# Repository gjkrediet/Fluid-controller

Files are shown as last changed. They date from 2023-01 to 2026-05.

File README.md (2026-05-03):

# Fluid-controller
A wireless battery powered pendant for FluidNC based on esp32



This controller uses bluetooth for communication. Be aware that bluetooth and wifi can not be used at the same time and, in fact, need different fluid-nc firmwares.  Sardar Azari seems to have adapted the controller to communicate via tcp. Take a look at https://github.com/AC8L/FluidNC-Pendant

# Main functions
Display shows: 
Machine coördinates, Work coördinates, Spindle speed and state, Set speed and step size when using joystick and rotation encoder, Overrides (Speed, Feed, Rapid),	Machine state, Battery state, Current buttons functions

Main functions buttons, joystick and dial: 
Wake up, Jog gantry and spindle via joystick and/or dial, Set Jog step size and speed via dial, Set spindle speed and switch on/off,	Set overrides (Speed, Feed, Rapid),	Cancel/abort job.

Main functions menu: 
Home machine, Zero workcoördinates, Go to zero, Probe.

# Hardware
1. LilyGO TTGO T-Display V1.1 which is a developmentboard with an ESP32, with a built-in tft (IPS) display and battery-charger. I purchased it for about €13 from internet.
2. Rotary encoder / dial (about €1)
3. Three colored buttons NO (total of €2)
4. PSP joystick (about €3)
5. Lion 18650 battery (€7)
6. Single-sided pcb
7. some pieces of wire (preferably different colors) of which five have female dupont-connectors
8. PLA (25 meter)
9. 8 screws M3 x 8

# Schematic and PCB

The pcb only holds the TTGO developmentboard and the rotary-encoder. The other components are mounted on the lid and wired to the pcb. The schematic of the pcb (in Kicad) is therefore very simple. The isolation-routing of the PCB was done with the very same CNC-router I made this controller for. To fit in the joystick, a corner of the PCB had to be sawed of (Later I updated the edge-cuts in Kicad so now the design should be OK).

The three buttons are at one side connected to the ground (all to J1.1) and are connected tot J1.2, J1.3 and J1.4 respectively.
The joystick is connected tot J2 with J2.2 unconnected (Because I later decided to wire the VCC of the joystick to an output-pin).

# Programming

Programming is done in Arduino IDE. All code exists in one single file. Most constants are enumerated or set with defines at the beginning. I hope it will explain itself to some extent.

Compile with partition scheme minimal SPIFFS or it will not fit.

# Case

pendantV2case_lid2
pendantV2lid_case

# Assembly

Schematic drawing of the lid with positioning of the components (excl. battery).

afbeelding

Female headers and the rotary encoder are soldered on the pcb. The other components are connected to the PCB with wires. Plus and minus wires are directly soldered to the battery and connected to the TTGO with a JST-connector.

inside1

To further reduce the powerconsumption I decided to feed the joystick via an outputpin of the esp32, which is why you see the red wire soldered on later.

inside2

The battery is wired to the JST-connector on the TTGO

# How to operate

The functions of the pendant were tailored to my needs. Below an oversight of the functions of the various buttons and button-combinations and the menu-options. It might be somewhat cryptic but I hope it may help.

JS=Joystick, BD=dial, BR=red button, BG=green button, BY=yellow button

Switch the pendant on: press JS

Reset the pendant: press JS

The pendant powers off after some time when idle or via the appropriate menu-option.

The pendant can either be in home-state (PH) or menu-state (PM).

Function of the dial-knob can be changed by rotating the dial while pressing BG.

Functions can be (default is DJ; function is indicated on the display with a blue circle):
- DX: Jog 1 step X-axis
- DY: Jog 1 step Y-axis
-	DZ: Jog 1 step Z-axis
-	DS: Set spindle-speed
-	DJ: set jogspeed and step-size
-	DOF: set override Feed
-	DOS: set override Speed
-	DOR: set override Rapid

The function of the buttons depend on the machine-state (MS, shown in the middle of the display of the pendant; function of BR, BG, BY shown on the bottom line of the display). They are as follows.

PH:
  -	JS + MS=Idle or MS=Jog:
    -	Up/down: jog Y-axis
    -	Left/Right: jog X-axis
  -	JS + MS=Idle or MS=Jog + BR (keep pressed)
    -	Up/down: jog Z-axis
    -	Left/Right: no function
  -	BG: enter PM
  -	BY: abort machine-operation
  -	BG (keep pressed) + BD: Change function dial-knob
  -	BR + MS=Alarm: Unlock Machine
  -	BR + DS: Spindle on/off

PM:
  -	BD: navigate menu (poweroff, spindlespeed, spindle on/off, small/large steps for changing jogspeed/stepsize, exit menu, home the machine, Set current Work XY-position to zero, Set current Work Z-position to zero, Probe Z-axis, Jog machine to XY-position zero, unlock Machine (grbl), reset Machine (grbl), Set and save brightness).
  -	BG: confirm menu-choice
  -	BR: Cancel
  -	BR (long press): poweroff

## OTA
Powering on the pendant while keeping the the red button pressed will start Wifi and activate OTA (Over The Air programming from within the Arduino IDE).

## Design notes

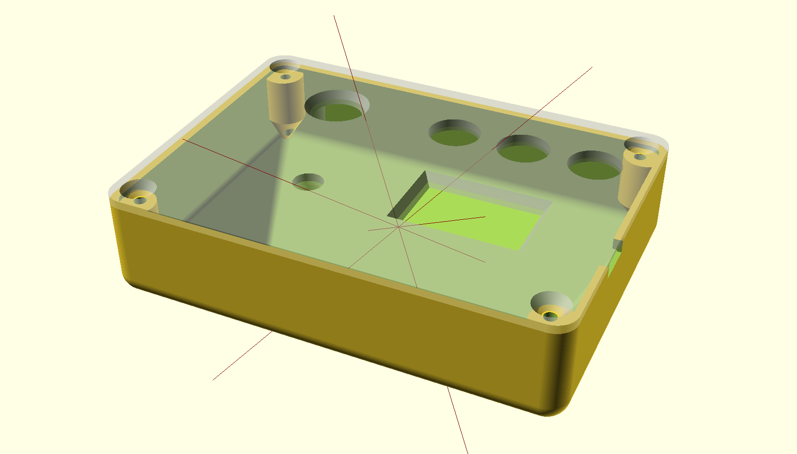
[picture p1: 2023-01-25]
case/pendantV2case_lid.png

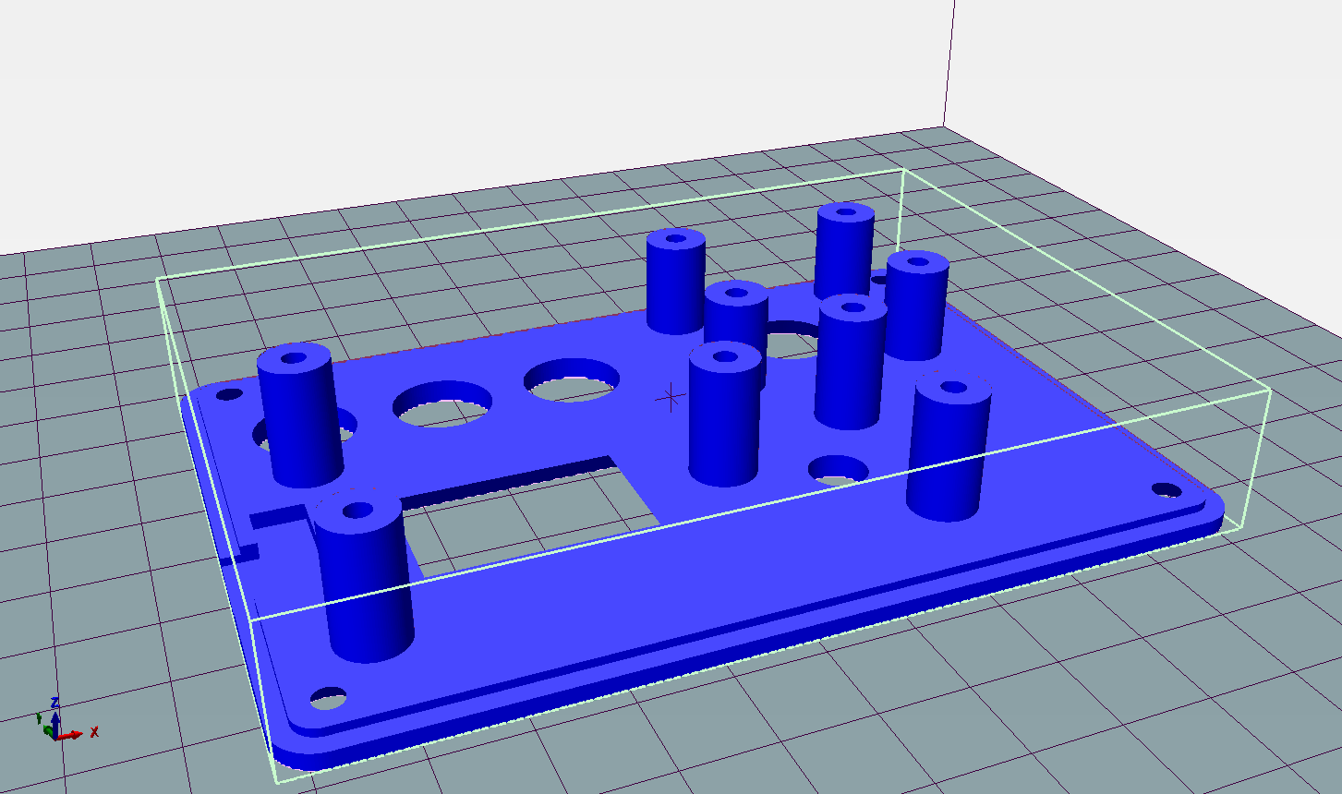
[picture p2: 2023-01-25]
case/pendantV2lid_stl.png

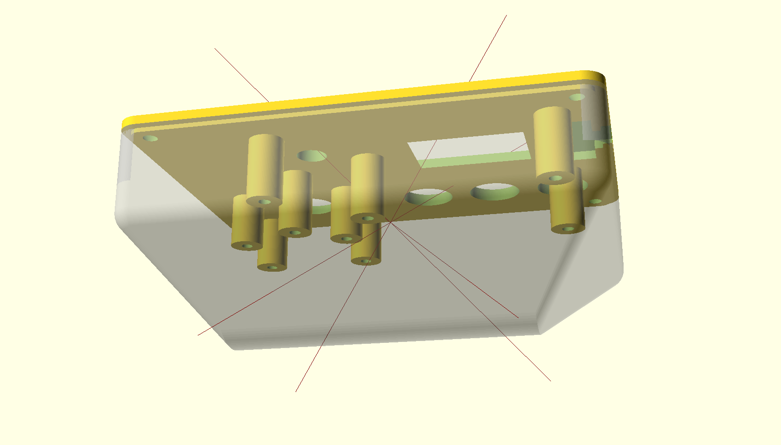
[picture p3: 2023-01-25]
case/pendantV2lid_case2.png

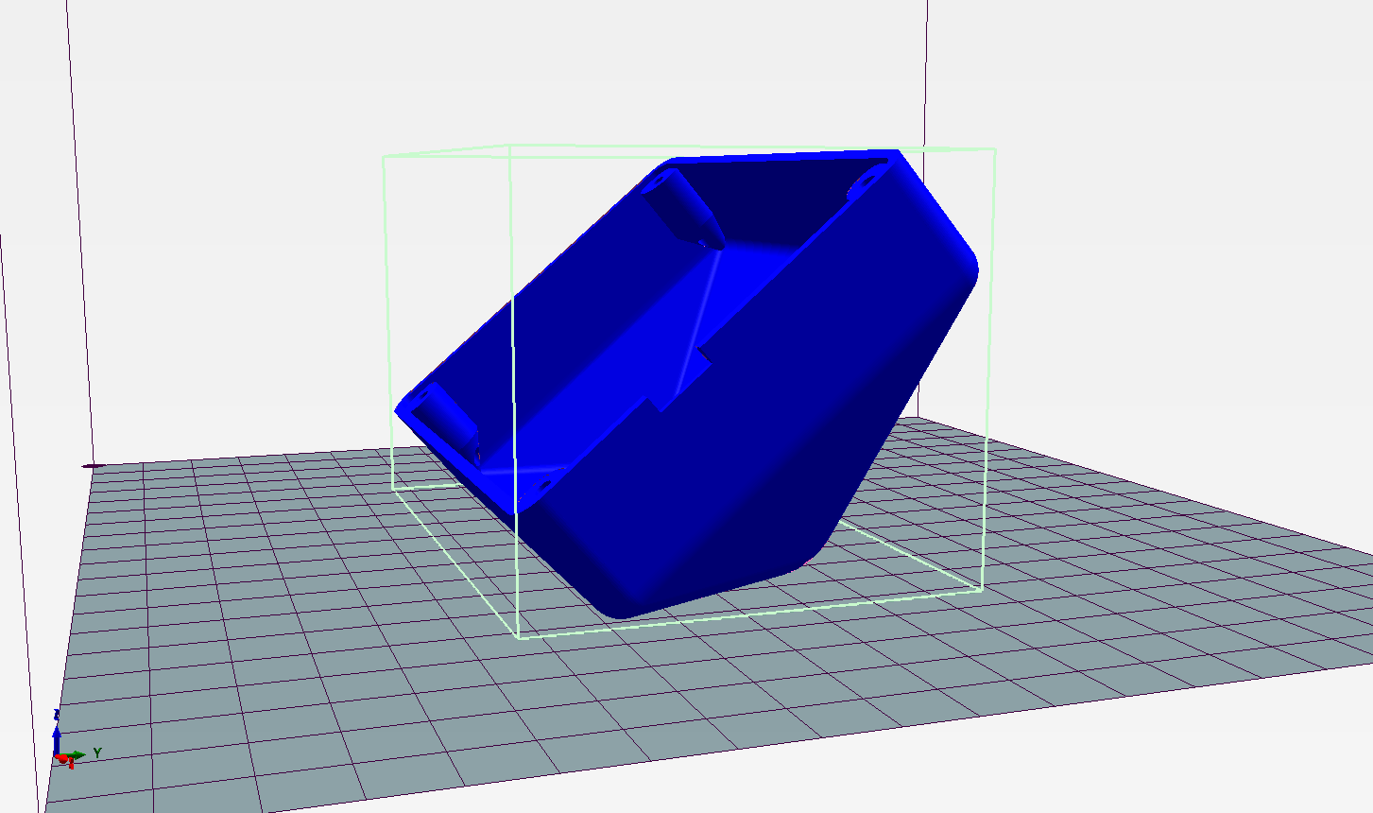
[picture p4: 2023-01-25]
case/pendantV2case_stl.png

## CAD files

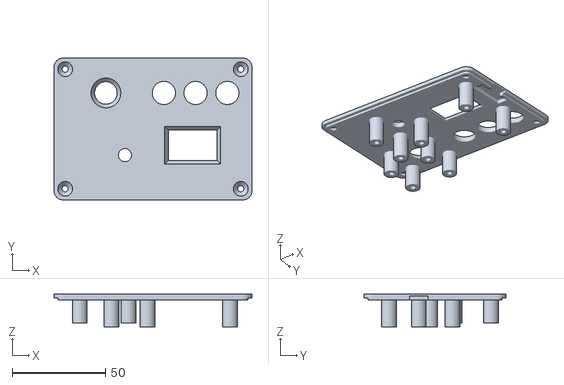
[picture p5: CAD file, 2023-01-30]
case/pendantV2lid.stl
106.0 x 76.0 x 17.5

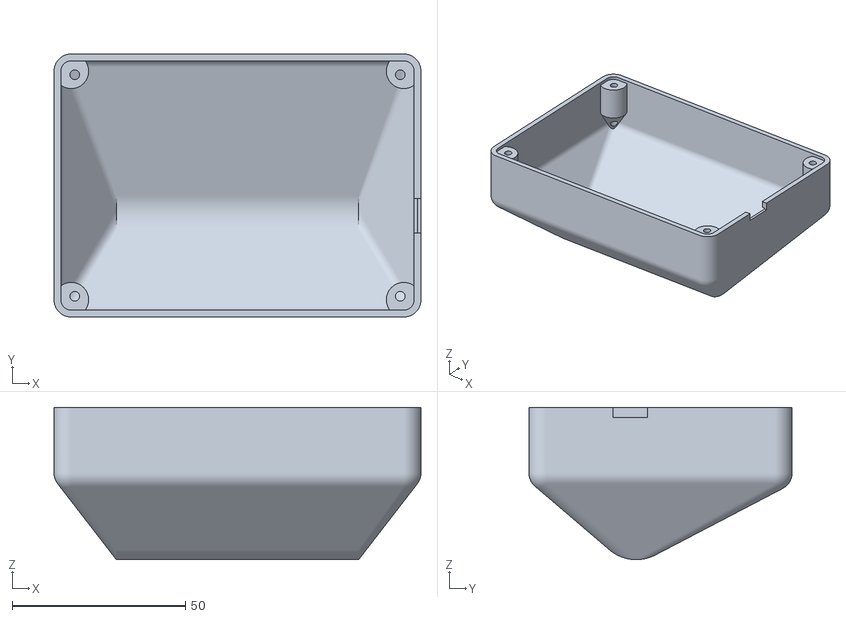
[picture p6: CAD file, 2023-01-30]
case/pendantV2case.stl
106.0 x 76.0 x 44.0

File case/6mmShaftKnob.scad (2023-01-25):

// copied and adapted from https://www.thingiverse.com/brunobruno

shaft_height = 8;
shaft_depth = 10;

width=30;
diameter_bottom_finish = 1;

extra_height = 0;
toprounding=-3;

shaft_clear = shaft_height-shaft_depth;
n = 12;
min_cap = 2;
height = shaft_height + min_cap + extra_height;
diameterBottom = width + diameter_bottom_finish;

$fn = 100;

difference(){
	intersection(){
		union(){
			cylinder(d=width,h=height,$fn=n);
			rotate(a=360/n/2,v=[0,0,1]) cylinder(d=width,h=height,$fn=n);
			// bottom finish
            cylinder(d=diameterBottom,h=2,$fn=50);
			translate([0,0,2]) cylinder(d1=diameterBottom,d2=0,h=10,$fn=50);
		};
		// top finish
        cylinder(d1=60,d2=width+toprounding,h=height);
	};
    // Shaft
#	difference(){
		union(){
			cylinder(d=6.2,h=shaft_height,$fn=50);
			cylinder(d1=6.7,d2=0,h=6.5,$fn=50);
		}
        translate([0,0, shaft_clear])
		translate([7,0,6]) cube([10,10,shaft_height-shaft_clear],center=true);
	}
}

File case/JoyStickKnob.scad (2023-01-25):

$fn=150;

intersection() {
    translate ([0,0,10]) cylinder (d=16,h=3,center=true);
    translate ([0,0,3]) sphere(d=20);
}

translate ([0,0,5]) difference() {
    cylinder (d1=7,d2=10,h=8,center=true);
    translate ([0,0,-1]) cylinder (d1=4.4,d2=4.2,h=6.1,center=true);
}

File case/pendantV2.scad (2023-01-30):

$fn=100;

$l=102;
$w=72;
$h1=19;
$d=6;
$dbat=20;

//remove the %-sign befor the next line to remove transparency
%union() {
    difference() {
        hull() {
            translate ([0,0,-10]) rotate([0,90,0]) cylinder (d=$dbat+4,h=70,center=true);
            translate ([0,7,($h1)/2]) hull () {
                translate ([($l-$d)/2, ($w-$d)/2,-($h1-$d)/2]) sphere(d=$d+4);
                translate ([($l-$d)/2, -($w-$d)/2,-($h1-$d)/2]) sphere(d=$d+4);
                translate ([-($l-$d)/2, ($w-$d)/2,-($h1-$d)/2]) sphere(d=$d+4);
                translate ([-($l-$d)/2, -($w-$d)/2,-($h1-$d)/2]) sphere(d=$d+4);
                translate ([($l-$d)/2, ($w-$d)/2,($h1-$d)/2+6]) cylinder(d=$d+4,h=0.01,center=true);
                translate ([($l-$d)/2, -($w-$d)/2,($h1-$d)/2+6]) cylinder(d=$d+4,h=0.01,center=true);
                translate ([-($l-$d)/2, ($w-$d)/2,($h1-$d)/2+6]) cylinder(d=$d+4,h=0.01,center=true);
                translate ([-($l-$d)/2, -($w-$d)/2,($h1-$d)/2+6]) cylinder(d=$d+4,h=0.01,center=true);
            }
        }
        difference() {
            hull() {
                translate ([0,0,-7]) rotate([0,90,0]) cylinder (d=$dbat,h=70,center=true);
                translate ([0,7,($h1)/2+0.1]) hull () {
                    translate ([($l-$d)/2, ($w-$d)/2,-($h1-$d)/2]) sphere(d=$d);
                    translate ([($l-$d)/2, -($w-$d)/2,-($h1-$d)/2]) sphere(d=$d);
                    translate ([-($l-$d)/2, ($w-$d)/2,-($h1-$d)/2]) sphere(d=$d);
                    translate ([-($l-$d)/2, -($w-$d)/2,-($h1-$d)/2]) sphere(d=$d);
                    translate ([($l-$d)/2, ($w-$d)/2,($h1-$d)/2+6]) cylinder(d=$d,h=0.01,center=true);
                    translate ([($l-$d)/2, -($w-$d)/2,($h1-$d)/2+6]) cylinder(d=$d,h=0.01,center=true);
                    translate ([-($l-$d)/2, ($w-$d)/2,($h1-$d)/2+6]) cylinder(d=$d,h=0.01,center=true);
                    translate ([-($l-$d)/2, -($w-$d)/2,($h1-$d)/2+6]) cylinder(d=$d,h=0.01,center=true);
                }
            }
        }
             //uitspring usb en print
        translate ([$l/2-1,-1.7,20.6]) cube([10,10,3],center=true);
        translate ([$l/2,-1.7,18]) cube([2,26,3],center=true);

    }

    //gaten schroeven
    translate ([0,7,0]) difference() {
        union () {
            hull() {
                translate ([$l/2-3, $w/2-3,14.9]) cylinder(d=10,h=12,center=true);
                translate ([$l/2-1, $w/2-1,0]) cylinder(d=1,h=1,center=true);
            }
            hull() {
                translate ([$l/2-3, -($w/2-3),14.9]) cylinder(d=10,h=12,center=true);
                translate ([$l/2-1, -($w/2-1),0]) cylinder(d=1,h=1,center=true);
            }
            hull() {
                translate ([-($l/2-3), -($w/2-3),14.9]) cylinder(d=10,h=12,center=true);
                translate ([-($l/2-1), -($w/2-1),0]) cylinder(d=1,h=1,center=true);
            }
            hull() {
                translate ([-($l/2-3), ($w/2-3),14.9]) cylinder(d=10,h=12,center=true);
                translate ([-($l/2-1), ($w/2-1),0]) cylinder(d=1,h=1,center=true);
            }
        }
        union () {
            translate ([$l/2-4, $w/2-4,11]) cylinder(d=2.8,h=20,center=true);
            translate ([-($l/2-4), $w/2-4,11]) cylinder(d=2.8,h=20,center=true);
            translate ([$l/2-4, -($w/2-4),11]) cylinder(d=2.8,h=20,center=true);
            translate ([-($l/2-4), -($w/2-4),11]) cylinder(d=2.8,h=20,center=true);
        }
    }
}

//deksel 3mm dik
//put a %-sign before the next line to make it transparent
translate ([0,14,0]) rotate ([0,0,180]) union() {
    translate ([0,7,9.5]) rotate([0,0,0]) difference() {
        union() {
    //delsel opdek deel
            translate ([0,0,1]) hull() {
                translate ([($l-$d)/2, ($w-$d)/2,($h1-$d)/2+6]) cylinder(d=$d+4,h=2,center=true);
                translate ([($l-$d)/2, -($w-$d)/2,($h1-$d)/2+6]) cylinder(d=$d+4,h=2,center=true);
                translate ([-($l-$d)/2, ($w-$d)/2,($h1-$d)/2+6]) cylinder(d=$d+4,h=2,center=true);
                translate ([-($l-$d)/2, -($w-$d)/2,($h1-$d)/2+6]) cylinder(d=$d+4,h=2,center=true);
            }   
    //deksel ingelaten deel
            hull() {
                translate ([($l-$d)/2, ($w-$d)/2,($h1-$d)/2+6]) cylinder(d=$d-0.3,h=2,center=true);
                translate ([($l-$d)/2, -($w-$d)/2,($h1-$d)/2+6]) cylinder(d=$d-0.3,h=2,center=true);
                translate ([-($l-$d)/2, ($w-$d)/2,($h1-$d)/2+6]) cylinder(d=$d-0.3,h=2,center=true);
                translate ([-($l-$d)/2, -($w-$d)/2,($h1-$d)/2+6]) cylinder(d=$d-0.3,h=2,center=true);
            }

        }
    //gaten schroeven
        
        translate ([$l/2-4, $w/2-4,13]) cylinder(d1=3.2,d2=8,h=3.1,center=true);
        translate ([-($l/2-4), $w/2-4,13]) cylinder(d1=3.2,d2=8,h=3.1,center=true);
        translate ([$l/2-4, -($w/2-4),13]) cylinder(d1=3.2,d2=8,h=3.1,center=true);
        translate ([-($l/2-4), -($w/2-4),13]) cylinder(d1=3.2,d2=8,h=3.1,center=true);

    //rotary encoders
        translate ([15,14,13]) cylinder(d=7,h=3.1,center=true);

    //venster scherm
        translate ([-21.2,8.7,11.5]) hull () {
            cube([26,16,0.1],center=true);
            translate ([0,0,3.1]) cube([30,20,0.1],center=true);
        }
    //gat joystick
        translate ([25.2,-19.3,13]) cylinder (d1=12,d2=16,h=3.1,center=true);
    //gaten drukknoppen
        translate ([-5.8,-19.3,13]) cylinder (d=12.4,h=3.1,center=true);
        translate ([-22.8,-19.3,13]) cylinder (d=12.4,h=3.1,center=true);
        translate ([-39.8,-19.3,13]) cylinder (d=12.4,h=3.1,center=true);
     //uitspring usb en knopjes
        translate ([-$l/2+2.8,8.7,12]) cube([10,10,3],center=true);
        translate ([-$l/2+5,8.7,12]) cube([6,22,3],center=true);

    }
    //pilaren joystick
    translate ([26.2,-13.3,14.8]) union() {
        translate ([13,9.75,0]) difference () {
            cylinder (d=8,h=12.6,center=true);
            cylinder (d=2.8,h=13.1,center=true);
        }
        translate ([13,-9.75,0]) difference () {
            cylinder (d=8,h=12.6,center=true);
            cylinder (d=2.8,h=13.1,center=true);
        }
        translate ([-13,-9.75,0]) difference () {
            cylinder (d=8,h=12.6,center=true);
            cylinder (d=2.8,h=13.1,center=true);
        }
        translate ([-13,9.75,0]) difference () {
            cylinder (d=8,h=12.6,center=true);
            cylinder (d=2.8,h=13.1,center=true);
        }
    }

    //pilaren printplaat
    translate ([0,7,13.8]) union() {
        translate ([22.3,24.6,0]) difference () {
            cylinder (d=8,h=14.5,center=true);
            cylinder (d=2.8,h=14.6,center=true);
        }
        translate ([22.3,2.6,0]) difference () {
            cylinder (d=8,h=14.5,center=true);
            cylinder (d=2.8,h=14.6,center=true);
        }
        translate ([2.9,8.7,0]) difference () {
            cylinder (d=8,h=14.5,center=true);
            cylinder (d=2.8,h=14.6,center=true);
        }
        translate ([-41.2,-9.3,0]) difference () {
            cylinder (d=8,h=14.5,center=true);
            cylinder (d=2.8,h=14.6,center=true);
        }
        translate ([-41.3,24.6,0]) difference () {
            cylinder (d=8,h=14.5,center=true);
            cylinder (d=2.8,h=14.6,center=true);
        }
    }
}

//    translate ([0,7,13]) cube ([110,60,18], center=true);
//    translate ([0,0,-7]) rotate([0,90,0]) cylinder (d=$dbat,h=110,center=true);

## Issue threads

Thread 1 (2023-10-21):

Getting started and Choosing the right hardware

cvjensen, 2023-10-21:
Hi @gjkrediet ,

I want to try to recreate your controller so before I order everything I hoped you would take a look and verify that its the right components I've found. I dont know how long the aliexpress links works so i've added some images just in case someone else sees this.

- **LilyGO TTGO T-Display V1.1 which is a developmentboard with an ESP32, with a built-in tft (IPS) display and battery-charger. I purchased it for about €13 from internet.**
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
[link](https://www.aliexpress.com/item/1005003745502352.html?spm=a2g0o.cart.0.0.202b38daKSeNMR&mp=1)

- **Rotary encoder / dial (about €1)**
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
[link](https://www.aliexpress.com/item/1005005973850924.html?spm=a2g0o.cart.0.0.202b38daKSeNMR&mp=1)

- **Three simple colored buttons NO (total of €2)**
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
[link](https://www.aliexpress.com/item/1005005904666959.html?spm=a2g0o.order_list.order_list_main.11.49011802j2I8of)

- **PSP joystick (about €3)**
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
[link](https://www.aliexpress.com/item/1005005985509291.html?spm=a2g0o.cart.0.0.202b38daKSeNMR&mp=1)

- **Pin bases for the pcb**
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
[link](https://www.aliexpress.com/item/1005006043456317.html?spm=a2g0o.cart.0.0.202b38daKSeNMR&mp=1)

- **Single-sided pcb**
I just uploaded the file to pcbway. Are the defaults alright?
sorry if I seem a little stupid. I've never tried ordering a pcb before 😄

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

I have 18650 laying around and tons of filament.
Anything else? It's just so annoying ordering everything, waiting 6 weeks and realizing you forgot something.

One more thing. Maybe before I order we could change the pcb so there's room for the joystick 😉

gjkrediet, 2023-10-21:
Hi @cvjensen. For the most part your list looks allright. The rotary encoder should be one that can be soldered on the pcb like this:
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
The 'pin bases' from your picture are what I call, female pcb-headers. You are correct that these should be soldered on the pcb. You should also have some M3 screws and some wires of which 5 have 'dupont' connectors. You could perhaps best use pre-made wires with dupont-connectors like these:
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
I always keep my pcb's simple and make the myself. I isolation-routed the connections on a single-sided PCB. I can imagine there is a learning-curve there, so maybe its easier to outsource it. I have no experience whatsoever whith that. So you are on your own there. Sorry.
I will take a look at the pcb-design though next week, also because the diameter of the various holes in the design might not be correct. So please have some patience with that.

cvjensen, 2023-10-22:
Thanks for the answer. I've now changed the encoder. And sorry I forgot to mention that I have dupont cables and M3's 😄

Then I guess I can order all the hardware right away and then I can order the PCB next week if you get the time to make the changes .

If you want to you could update the readme with pictures of the hardware.
I guess it would make it a little easier for the next one that wants to replicate it.

gjkrediet, 2023-10-23:
@cvjensen thanks for your tips. I have updated the edge-cuts of the PCB. The size of the holes seems to be OK. The pads are quite large (to best facilitate edge-routing). Please let me know if this works out OK in the end-result.

cvjensen, 2023-10-23:
@gjkrediet I dont see any recent changes in the files. Remembered to git commit and git upload?

gjkrediet, 2023-10-23:
@cvjensen you are right. There's a bit of a learning curve with Github. Committed it just now.

cvjensen, 2023-10-24:
@gjkrediet thanks - I'll test it out in about a month when everything arrives 😄

cvjensen, 2023-10-24:
@gjkrediet apparently I need a gerber file to order from pcbway. I'm getting this error:

The file can not be opened, please upload Gerber files in format of RS-274x.;

Anything you are familiar with?

gjkrediet, 2023-10-24:
@cvjensen In Kicad you can create gerber-files. If you don't have Kicad you can download it for free. To create a gerber-file you can ignore all the possibilities of Kicad. Just load the PCB-file in Kicad and select pcb-editor->file->plot.
There are many options concerning the format of Gerber, but i do not know which you have to choose for pcbway. I have no experience with PCB-manufacturers but many others do have. There is a Kicad-forum and from what I gathered it also discusses options and problems related to pcbway. Could you first take a look there? Let me know if you get stuck.

cvjensen, 2023-11-21:
Hi again  @gjkrediet , I'm in the middle of building the controller now. The PCB's i received seems fine but i cannot tell if they work yet. So far the only problem i've come across is this:

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

as you can see i've melted the standoff with my soldering iron to get room for the esp.
but it works now.

What doesnt work and are driving me crazy is when i try to verify and compile:

```
Arduino: 1.8.19 (Windows 10), Board: "TTGO T7 V1.4 Mini32, Default 4MB with spiffs (1.2MB APP/1.5MB SPIFFS), 240MHz (WiFi/BT), QIO, 80MHz, 4MB (32Mb), 921600, None, Disabled"

C:\Users\user\Downloads\Fluid-controller-main (1)\Fluid-controller-main\arduino\PendantV2_45\PendantV2_45.ino: In function 'void setup()':

PendantV2_45:171:17: error: 'TFT_BL' was not declared in this scope

   ledcAttachPin(TFT_BL, 0); // TFT_BL, 0 - 15

                 ^~~~~~

C:\Users\user\Downloads\Fluid-controller-main (1)\Fluid-controller-main\arduino\PendantV2_45\PendantV2_45.ino:171:17: note: suggested alternative: 'TFT_BLUE'

   ledcAttachPin(TFT_BL, 0); // TFT_BL, 0 - 15

                 ^~~~~~

                 TFT_BLUE

C:\Users\user\Downloads\Fluid-controller-main (1)\Fluid-controller-main\arduino\PendantV2_45\PendantV2_45.ino: In function 'void activeTimer(bool)':

PendantV2_45:1129:20: error: 'TFT_BL' was not declared in this scope

       digitalWrite(TFT_BL, LOW);

                    ^~~~~~

C:\Users\user\Downloads\Fluid-controller-main (1)\Fluid-controller-main\arduino\PendantV2_45\PendantV2_45.ino:1129:20: note: suggested alternative: 'TFT_BLUE'

       digitalWrite(TFT_BL, LOW);

                    ^~~~~~

                    TFT_BLUE

PendantV2_45:1130:24: error: 'TFT_DISPOFF' was not declared in this scope

       tft.writecommand(TFT_DISPOFF);

                        ^~~~~~~~~~~

C:\Users\user\Downloads\Fluid-controller-main (1)\Fluid-controller-main\arduino\PendantV2_45\PendantV2_45.ino:1130:24: note: suggested alternative: 'TFT_INVOFF'

       tft.writecommand(TFT_DISPOFF);

                        ^~~~~~~~~~~

                        TFT_INVOFF

PendantV2_45:1131:24: error: 'TFT_SLPIN' was not declared in this scope

       tft.writecommand(TFT_SLPIN);

                        ^~~~~~~~~

C:\Users\user\Downloads\Fluid-controller-main (1)\Fluid-controller-main\arduino\PendantV2_45\PendantV2_45.ino:1131:24: note: suggested alternative: 'TFT_eSPI'

       tft.writecommand(TFT_SLPIN);

                        ^~~~~~~~~

                        TFT_eSPI

Multiple libraries were found for "WiFi.h"

 Used: C:\Users\user\AppData\Local\Arduino15\packages\esp32\hardware\esp32\2.0.11\libraries\WiFi

 Not used: C:\Program Files (x86)\Arduino\libraries\WiFi

exit status 1

'TFT_BL' was not declared in this scope

This report would have more information with
"Show verbose output during compilation"
option enabled in File -> Preferences.

```

which tft module are you using?
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
cvjensen, 2023-11-22:
Alright one step closer . Change some settings in arduino regarding flash size.

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

So now I have to change the following I guess?

```
const char *ssid = "yourssid";
const char *password = "yourpassword";
```

cvjensen, 2023-11-22:
I was hoping I could use the remote with bt connection directly to the fluidnc, but I can see here that:
[You will not see the Bluetooth options while using the WiFi firmware.](http://wiki.fluidnc.com/en/features/wifi_bt)

Will I be able to connect it to my home network and then it can talk to fluidnc that way through? Or do I really have to isolate fluidnc from my home network?

cvjensen, 2023-11-22:
I dont seem to get anything in the serial monitor

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

The only thing i can do to get any response is pressing the joystick , that turns on the screen , but again nothing in the console ?

gjkrediet, 2023-11-22:
FLuidnc cannot use both bluetooth and wifi. Perhaps there is a way that I do not know of. I use my setup via usb and via bluetooth.
Maybe it is possible to change the controller-program so that it communicates via wifi/telnet. I remember there was a discussion about it. There might be people on github or discord who can shed a light on this.
But first it would be nice if you got your controller working. You were right to use a different memory-organisation (minimal spiffs). I mentioned that in the descriptions but it is easy to miss.
The ssid/password are only used for uploading via OTA.
When you reset fluidnc via the terminal/usb do you get a message in the output like: "BT started with FluidNC"?

cvjensen, 2023-11-22:
Alright so i have to chose between bluetooth which is the only way the controller can talk to fluidnc and WiFi theres the only way that my pc can talk to fluidnc (fluid nc is in my case a laser engraver and later perhaps also a plasma cutter in my garage . None of it i want inside in my office).. so that is going to be a problem .
Perhaps i should try to dig after who mentioned something with wifi connection. I remember to have read it also at some point.

So far i do not have seen anything in the console. Can i reset it in any other way than the buttons on the board or the battery ?

cvjensen, 2023-11-23:
Found it here https://github.com/AC8L/FluidNC-Pendant

cvjensen, 2023-11-23:
Okay i've managed to get it up and running with the wifi firmware. I dont seem to have any working buttons but ill take a look at it later. Thanks for the help so far! 😄

gjkrediet, 2023-11-23:
That’s great! Good to know there is someone out there who already solved this problem. I will link this it in my readme.

Enjoy your controller!

Van: cvjensen ***@***.***>
Verzonden: donderdag 23 november 2023 11:35
Aan: gjkrediet/Fluid-controller ***@***.***>
CC: Gertjan Krediet ***@***.***>; Mention ***@***.***>
Onderwerp: Re: [gjkrediet/Fluid-controller] Getting started and Choosing the right hardware (Issue #1)

Okay i've managed to get it up and running with the wifi firmware. I dont seem to have any working buttons but ill take a look at it later. Thanks for the help so far! 😄

—
Reply to this email directly, view it on GitHub <https://github.com/gjkrediet/Fluid-controller/issues/1#issuecomment-1824163689> , or unsubscribe <https://github.com/notifications/unsubscribe-auth/AE2WOFP2UBS74P5RAEDZF4DYF4REXAVCNFSM6AAAAAA6KFDBOGVHI2DSMVQWIX3LMV43OSLTON2WKQ3PNVWWK3TUHMYTQMRUGE3DGNRYHE> .
You are receiving this because you were mentioned.Message ID: ***@***.***>

gjkrediet, 2023-11-23:
Let me know if I can help with the button-problem.

Van: cvjensen ***@***.***>
Verzonden: donderdag 23 november 2023 11:35
Aan: gjkrediet/Fluid-controller ***@***.***>
CC: Gertjan Krediet ***@***.***>; Mention ***@***.***>
Onderwerp: Re: [gjkrediet/Fluid-controller] Getting started and Choosing the right hardware (Issue #1)

Okay i've managed to get it up and running with the wifi firmware. I dont seem to have any working buttons but ill take a look at it later. Thanks for the help so far! 😄

—
Reply to this email directly, view it on GitHub <https://github.com/gjkrediet/Fluid-controller/issues/1#issuecomment-1824163689> , or unsubscribe <https://github.com/notifications/unsubscribe-auth/AE2WOFP2UBS74P5RAEDZF4DYF4REXAVCNFSM6AAAAAA6KFDBOGVHI2DSMVQWIX3LMV43OSLTON2WKQ3PNVWWK3TUHMYTQMRUGE3DGNRYHE> .
You are receiving this because you were mentioned.Message ID: ***@***.***>

Closed 2023-11-23.

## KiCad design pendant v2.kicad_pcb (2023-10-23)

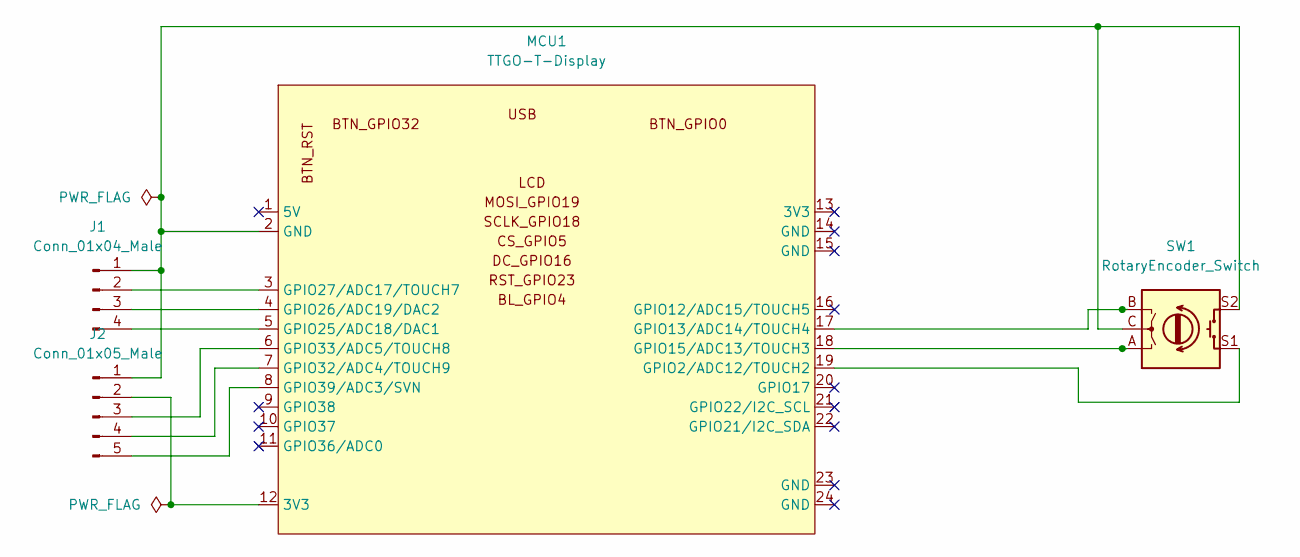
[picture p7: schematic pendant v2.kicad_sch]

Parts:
J1: Conn_01x04_Male; PinHeader_1x04_P2.54mm_Vertical
J2: Conn_01x05_Male; PinHeader_1x05_P2.54mm_Vertical
MCU1: TTGO-T-Display
SW1: RotaryEncoder_Switch; RotaryEncoder_Alps_EC12E-Switch_Vertical_H20mm

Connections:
unnamed: J1.1, J2.1, MCU1.2 (GND), SW1.C, SW1.S2
unnamed: J1.2, MCU1.3 (GPIO27/ADC17/TOUCH7)
unnamed: J1.3, MCU1.4 (GPIO26/ADC19/DAC2)
unnamed: J1.4, MCU1.5 (GPIO25/ADC18/DAC1)
unnamed: J2.3, MCU1.6 (GPIO33/ADC5/TOUCH8)
unnamed: J2.4, MCU1.7 (GPIO32/ADC4/TOUCH9)
unnamed: J2.5, MCU1.8 (GPIO39/ADC3/SVN)
unnamed: J2.2, MCU1.12 (3V3)
unnamed: MCU1.17 (GPIO13/ADC14/TOUCH4), SW1.B
unnamed: MCU1.18 (GPIO15/ADC13/TOUCH3), SW1.A
unnamed: MCU1.19 (GPIO2/ADC12/TOUCH2), SW1.S1

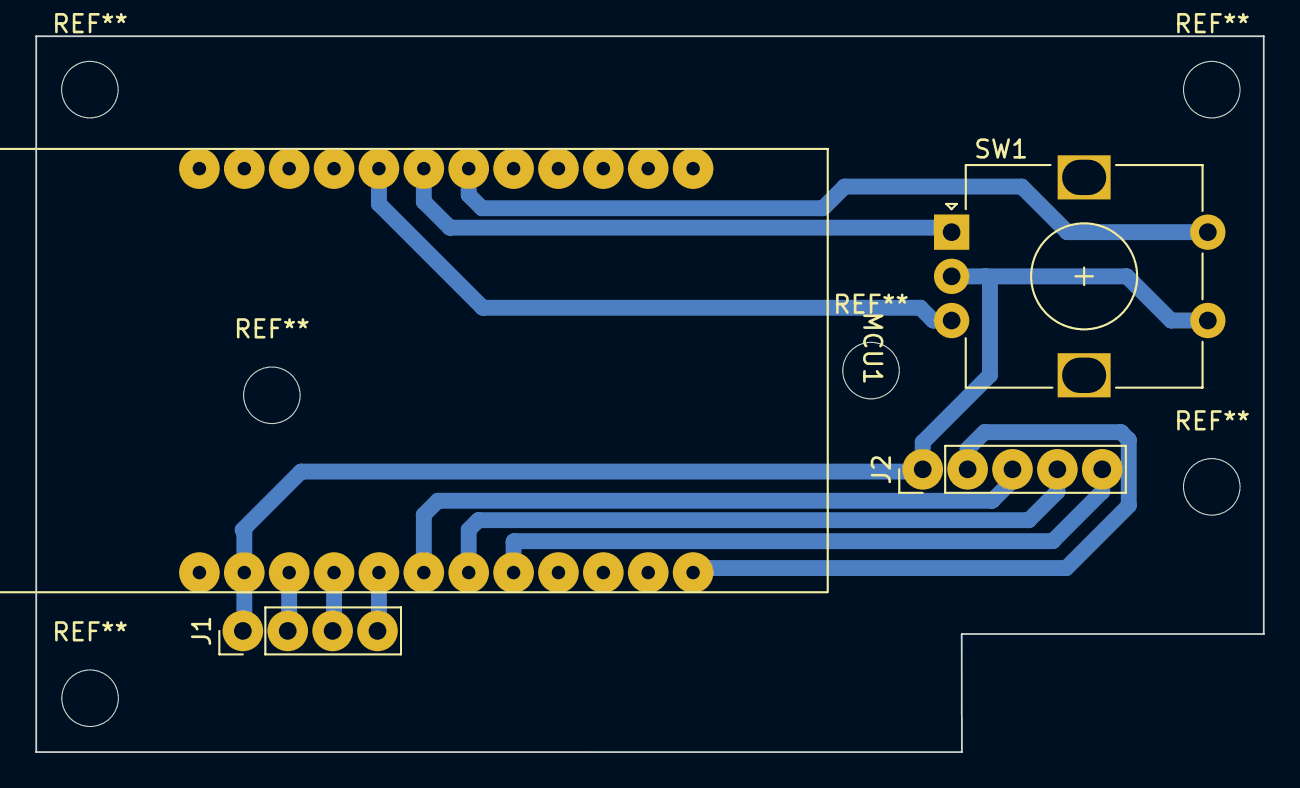
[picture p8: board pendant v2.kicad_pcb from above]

Board: 2 copper layers, 69.5 x 40.5 mm, 4 parts (0 on the bottom side), 11 nets.

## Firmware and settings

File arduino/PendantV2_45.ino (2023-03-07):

#include "BluetoothSerial.h"
#if !defined(CONFIG_BT_SPP_ENABLED)
#error Serial Bluetooth not available or not enabled. It is only available for the ESP32 chip.
#endif
#include <Wire.h>
#include <RotaryEncoder.h>
#include <PinButton.h>
#include <WiFi.h>
#include <ArduinoOTA.h>
#include <EEPROM.h>
#include <esp_wifi.h>
#include <TFT_eSPI.h>      // Hardware-specific library

#define EEPROM_SIZE 1

TFT_eSPI tft = TFT_eSPI(); // Invoke custom library

BluetoothSerial SerialBT;
RotaryEncoder *encoderA = nullptr;

// I/O pindefinitions
#define PIN_REM1 GPIO_NUM_13
#define PIN_REM2 GPIO_NUM_15
#define PIN_JSX GPIO_NUM_32
#define PIN_JSY GPIO_NUM_33
#define PIN_REMS GPIO_NUM_2
#define PIN_YELLOW GPIO_NUM_25
#define PIN_GREEN GPIO_NUM_26
#define PIN_RED GPIO_NUM_27
#define PIN_JS_VCC GPIO_NUM_17
#define PIN_BATT 34
#define ADC_EN  14

#define TFT_LEFT    1
#define TFT_CENTER  2
#define TFT_RIGHT   3
#define TFT_TRANSP  true
#define TFT_OBLQ  false
#define TFT_LIGHTBLUE 0x86FF
#define TFT_LIGHTRED 0xF9E7
#define TFT_DARKBLUE 0x0018
#define TFT_OVERYELLOW 0xFF35
#define TFT_MEDIUMGREEN 0x04A2
#define TFT_DARKRED 0xA800
#define TFT_MEDIUMBLUE 0x3D5F
#define TFT_DARKORANGE 0xFAC0

#define MAX_JOGSTR 50
#define MAX_STATUSSTR 50
#define POWEROFF_TIME 300
#define LINEHEIGHT_DEF  22

enum machinestate {
  Unknwn,
  Alarm,
  Idle,
  Jog,
  Home,
  Check,
  Run,
  Cycle,
  Hold,
  Door,
  Sleep
};
enum pendantstate {
  Menu,
  MenuConfirm,
  Pendant,
  RotateChoice,
  MenuSpindleSpeed,
  MenuBrightness
};

enum menuOptions {
  poweroff,
  spindlespeed,
  spindleonoff,
  steps,
  quit,
  home,
  setwxy0,
  setwz0,
  probe,
  gawxy0,
  unlock,
  resetgrbl,
  brightness
};

enum rotorDestin  {
  RotXaxis,
  RotYaxis,
  RotZaxis,
  RotSpindlespeed,
  RotJogspeed,
  RotOvfeed,
  RotOvspeed,
  RotOvrapid
};

enum joystickDestin {
  jsXYaxis,
  jsZaxis
};

machinestate mState = Unknwn;
pendantstate pState = Pendant;
menuOptions menuState = quit;
rotorDestin rState = RotJogspeed;
joystickDestin jState = jsXYaxis;

const int maxMenu = 12;
const int jogSpeedMax = 5000; //dit moet gelijk lopen met de settings in config.yaml
static char mStateStr[][11] { "? ?", "ALARM", "IDLE", "JOG", "HOME", "CHECK", "RUN", "CYCLE", "HOLD", "SAFE", "SLEEP" };
const int powerOffTime = 60;
bool powerOffNow = false;

String name = "FluidNC";
//String name = "btgrblesp";
//uint8_t address[6]  = {0xA5, 0xFE, 0x06, 0x00, 0xFF, 0xFF};
//uint8_t address[6] = {0x00, 0x00, 0x00, 0x00, 0x00, 0x00};
//uint8_t address[6] = {0xC8, 0xC9, 0xA3, 0xD2, 0xA5, 0xFE};
bool btConnected;
const char *ssid = "yourssid";
const char *password = "yourpassword";


char jogStr[MAX_JOGSTR];
char statusStr[MAX_STATUSSTR];
char sbuf[20];
byte menuChoice = 0, backLight = 1;
unsigned long lastJogCmdXYZ = 0, lastStepCmdXYZ = 0;
const int tExec = 1000;
const int updateInterval = 198;
float distX = 0, distY = 0, distZ = 0;
int battVolt;
unsigned long sinceStart, lastGrblState;
int rdX = 0, rdY = 0, rdZ = 0, multXYZ = 0;
int calibrateX, calibrateY;
float mX, mY, mZ;  //Machine positions
float wX, wY, wZ;  //Work positions
RTC_DATA_ATTR int jogSpeed = 1000; //Overleeft een herstart vanuit sleep
int jogSpeedDisp = 0, setSpindleSpeed = 3000, spindleDisp = -1;
int reportedSpindleSpeed = 0;
int ovSpeed = 0, ovFeed = 0, ovRapid = 0;
bool spindleOn = false;
String grblState;
bool smallSteps = false;
int stepXYZ = 0;
PinButton buttonREMS(PIN_REMS);
PinButton buttonGREEN(PIN_GREEN);
PinButton buttonYELLOW(PIN_YELLOW);
PinButton buttonRED(PIN_RED);

void setup() {
  //  setCpuFrequencyMhz(240);
  Serial.begin(115200);
  EEPROM.begin(EEPROM_SIZE);
  pinMode(ADC_EN, OUTPUT);
  digitalWrite(ADC_EN, HIGH);
  analogReadResolution(9);  //minimum is 9 bits dus waarden 0 en 512;
  backLight = EEPROM.read(0) % 16;
  if (backLight < 1) backLight = 1;
  tft.init();
  tft.setRotation(3);
  tft.fillScreen(TFT_BLACK);
  //zet de helderheid van het backlight
  ledcSetup(0, 5000, 8); // 0-15, 5000, 8
  ledcAttachPin(TFT_BL, 0); // TFT_BL, 0 - 15
  ledcWrite(0, 64); // 0-15, 0-255 (with 8 bit resolution)
  tftPrintSimple(20, 2 * LINEHEIGHT_DEF, "(OTA)");
  tftPrintSimple( 20, 3 * LINEHEIGHT_DEF, "Connecting...");
  if (digitalRead(PIN_RED) == LOW) otaLoop();
  ledcWrite(0, backLight * backLight); // 0-15, 0-255 (with 8 bit resolution)
  pinMode(PIN_JSX, INPUT);
  pinMode(PIN_JSY, INPUT);
  pinMode(PIN_BATT, INPUT);
  pinMode(PIN_REMS, INPUT_PULLUP);
  //  pinMode(PIN_JSS,INPUT_PULLUP);
  pinMode(PIN_JS_VCC, OUTPUT);
  digitalWrite(PIN_JS_VCC, HIGH);
  grblState.reserve(100);
  tftUpdate(true);
  /*
    xTaskCreatePinnedToCore(Task1code,"Task1",10000,NULL,1,&Task1,0);
    vTaskDelay(500);
  */
  encoderA = new RotaryEncoder(PIN_REM1, PIN_REM2, RotaryEncoder::LatchMode::FOUR3);
  // register interrupt routine
  attachInterrupt(digitalPinToInterrupt(PIN_REM1), checkPositionA, CHANGE);
  attachInterrupt(digitalPinToInterrupt(PIN_REM2), checkPositionA, CHANGE);
  activeTimer(true);
  // Calibrate Joystick
  for (int n = 100; n; --n) {
    calibrateX += analogRead(PIN_JSX);
    calibrateY += analogRead(PIN_JSY);
    delay(1);
  }
  calibrateX /= 100;
  calibrateY /= 100;
  Serial.println("The device started in master mode, make sure remote BT device is on!");
  SerialBT.begin("ESP32test", true);
  SerialBT.setTimeout(5000);
  SerialBT.register_callback(btCallback);
  if (!SerialBT.connect(name)) {
    tftPrint(TFT_LEFT, TFT_OBLQ, TFT_RED, TFT_BLACK, 20, 2 * LINEHEIGHT_DEF, 0, "No connection");
    tftPrint(TFT_LEFT, TFT_OBLQ, TFT_RED, TFT_BLACK, 20, 3 * LINEHEIGHT_DEF, 0, "Shutting down");
    delay(2000);
    esp_deep_sleep_start();
  }
  Serial.println("Connected Succesfully to " + name);
  getGrblState(false);
}


void otaLoop() {
  WiFi.mode(WIFI_STA);
  WiFi.begin(ssid, password);
  tft.fillScreen(TFT_BLACK);
  tftPrintSimple( 0, 1 * LINEHEIGHT_DEF, "WiFi");
  while (WiFi.status() != WL_CONNECTED) {
    delay(500);
  }
  Serial.println(WiFi.localIP());
  tftPrintSimple( 0, 2 * LINEHEIGHT_DEF, "OTA");
  ArduinoOTA.setHostname("ESP32-pendant");
  ArduinoOTA.begin();
  while (true) {
    ArduinoOTA.handle();
    delay(1000);
    checkBattery();
    sprintf(sbuf, "Batt: %d", (int) battVolt);
    tftPrintSimple( 100, 4 * LINEHEIGHT_DEF, sbuf);
  }
}

IRAM_ATTR void checkPositionA() {
  encoderA->tick();  // just call tick() to check the state.
}

void forceEndJog() {
  Serial.println("C");
  btWrite(0x85);
  //  Serial.println("cancel");
  delay(100);
  getGrblState(false);
  while (mState == Jog) {
    Serial.println("D");
    btWrite(0x85);
    //    Serial.println("cancel");
    delay(100);
    getGrblState(true);
  }
}

void btWrite(char c) {
  if (btConnected) {
    SerialBT.write(c);
  }
  else mState = Unknwn;
}

void waitEndJog() {
  getGrblState(false);
  while (mState == Jog) {
    delay(100);
    getGrblState(true);
    //    Serial.print("jog wait...");
    //    Serial.println(mState);
  }
}

const int rdRawMin = -30;
const int rdRawMax = 30;
const int hysteresis = 10;

int readJSX() {
  int rdRaw = 0;
  for (int n = 10; n; --n) {
    rdRaw += analogRead(PIN_JSX) - calibrateX;
  }
  rdRaw /= 10;
  // soft hysteresis
  if (rdRaw < rdRawMin + hysteresis && rdRaw > rdRawMin && rdX == -1) rdRaw = rdRawMin;
  else if (rdRaw > rdRawMax - hysteresis && rdRaw < rdRawMax && rdX == 1) rdRaw = rdRawMax;
  return (rdRaw);
}

int readJSY() {
  int rdRaw = 0;
  for (int n = 10; n; --n) {
    rdRaw += analogRead(PIN_JSY) - calibrateY;
  }
  rdRaw /= 10;
  // soft hysteresis
  if (rdRaw < rdRawMin + hysteresis && rdRaw > rdRawMin && rdY == 1) rdRaw = rdRawMin;
  else if (rdRaw > rdRawMax - hysteresis && rdRaw < rdRawMax && rdY == -1) rdRaw = rdRawMax;
  return (rdRaw);
}

int checkJoystick() {
  static int rdXprev = 0, rdYprev = 0, rdZprev = 0;
  static float sX, sY, sZ, speedXYZ;
  /*
    if (readJSY() <= rdRawMin || readJSY() >= rdRawMax ||
        readJSX() <= rdRawMin || readJSX() >= rdRawMax)
      checkConnectBt();
  */
  if (mState != Idle || pState != Pendant || rState == RotSpindlespeed) return 0;

  while (true) {
    sinceStart = millis() + tExec;
    checkRotateA();
    rdX = 0;
    rdY = 0;
    rdZ = 0;
    if (jState == jsZaxis) {
      if (readJSY() <= rdRawMin) rdZ = 1;
      else if (readJSY() >= rdRawMax) rdZ = -1;
    } else {
      if (readJSX() <= rdRawMin) rdX = -1;
      else if (readJSX() >= rdRawMax) rdX = 1;
      if (readJSY() <= rdRawMin) rdY = 1;
      else if (readJSY() >= rdRawMax) rdY = -1;
    }
    if (rdX == 0 && rdY == 0 && rdZ == 0) {
      if (mState == Jog) {
        forceEndJog();
        lastJogCmdXYZ = 0;
      }
      return 0;
    }
    activeTimer(true);
    if (rdX != rdXprev || rdY != rdYprev || rdZ != rdZprev) {
      rdXprev = rdX;
      rdYprev = rdY;
      rdZprev = rdZ;
      btWrite(0x85);
      lastJogCmdXYZ = 0;
    }
    if (sinceStart - lastGrblState > updateInterval) {
      //      Serial.println("A");
      getGrblState(true);
    }
    multXYZ = jogSpeed > jogSpeedMax ? jogSpeedMax : jogSpeed;
    if (sinceStart - lastJogCmdXYZ > tExec) {
      sX = abs(rdX * rdX) * multXYZ;
      sY = abs(rdY * rdY) * multXYZ;
      sZ = abs(rdZ * rdZ) * multXYZ;
      //      if (sX>=sY) sY=0; else sX=0; //alleen via X of via Y bewegen
      if (sZ) speedXYZ = sZ;
      else speedXYZ = sqrt(sX * sX + sY * sY);
      distX = ((jogSpeedMax - sX) / 200000000 + 0.000018) * sX * (rdX ? (rdX < 0 ? -1 : 1) : 0) * tExec;
      distY = ((jogSpeedMax - sY) / 200000000 + 0.000018) * sY * (rdY ? (rdY < 0 ? -1 : 1) : 0) * tExec;
      distZ = ((jogSpeedMax - sZ) / 200000000 + 0.000018) * sZ * (rdZ ? (rdZ < 0 ? -1 : 1) : 0) * tExec;
      snprintf(jogStr, MAX_JOGSTR, "$J=G21G91X%fY%fZ%fF%d", distX, distY, distZ, (int)speedXYZ);
      lastJogCmdXYZ = sinceStart;
      btPrintln(jogStr);
      Serial.println(jogStr);
      delay(10);
      getGrblState(true);
      mState = Jog; //force
    }
  }
}

void checkRotateA() {
  static int posPrev = 0, pos, dir;
  //  encoderA->tick(); // just call tick() to check the state.
  pos = encoderA->getPosition();
  if (posPrev == pos) return;
  activeTimer(true);
  posPrev = pos;
  dir = (int)encoderA->getDirection();
  if (pState == RotateChoice) {
    tftUpdate(true);
    if (dir == 1) {
      if (rState == RotOvrapid) rState = RotOvspeed;
      else if (rState == RotOvspeed) rState = RotOvfeed;
      else if (rState == RotOvfeed) rState = RotJogspeed;
      else if (rState == RotJogspeed) rState = RotSpindlespeed;
      else if (rState == RotSpindlespeed) rState = RotZaxis;
      else if (rState == RotZaxis) rState = RotYaxis;
      else rState = RotXaxis;
    } else {
      if (rState == RotXaxis) rState = RotYaxis;
      else if (rState == RotYaxis) rState = RotZaxis;
      else if (rState == RotZaxis) rState = RotSpindlespeed;
      else if (rState == RotSpindlespeed) rState = RotJogspeed;
      else if (rState == RotJogspeed) rState = RotOvfeed;
      else if (rState == RotOvfeed) rState = RotOvspeed;
      else rState = RotOvrapid;
    }
    tftUpdate(true);
  } else if (pState == Pendant && digitalRead(PIN_GREEN)==HIGH) {
    if (rState < 3 || pState == RotateChoice) { //een van de assen
      static unsigned long lastStepCmd = 0;
      float dist = 0;
      if (dir == 1) dist = 0.001 * (jogSpeed > 5000 ? 5000 : jogSpeed);
      else dist = -0.001 * (jogSpeed > 5000 ? 5000 : jogSpeed);
      switch (rState) {
        case RotZaxis:
          snprintf(jogStr, MAX_JOGSTR, "$J=G21G91X0Y0Z%fF%d", dist, 1000);
          break;
        case RotYaxis:
          snprintf(jogStr, MAX_JOGSTR, "$J=G21G91X0Y%fZ0F%d", dist, 1000);
          break;
        case RotXaxis:
          snprintf(jogStr, MAX_JOGSTR, "$J=G21G91X%fY0Z0F%d", dist, 1000);
          break;
        default:
          break;
      }
      if (pState == RotateChoice) snprintf(jogStr, MAX_JOGSTR, "$J=G21G91X0Y0Z%fF%d", dist, 1000);
      lastStepCmd = sinceStart;
      btPrintln(jogStr);
      Serial.println(jogStr);
      while (sinceStart - lastStepCmd < (20 + (jogSpeed > 5000 ? 5000 : jogSpeed) / 20)) {
        sinceStart = millis() + tExec;
        encoderA->tick();
      }
    }
    else if (rState == RotOvfeed) {
      btWrite(dir == 1 ? 0x91 : 0x92);
    }
    else if (rState == RotOvspeed) {
      btWrite(dir == 1 ? 0x9A : 0x9B);
    }
    else if (rState == RotOvrapid) {
      btWrite(dir == 1 ? (ovRapid < 50 ? 0x96 : 0x95) : (ovRapid > 50 ? 0x96 : 0x97));
    }
    else if (rState == RotSpindlespeed) {
      if (dir == 1) {
        if (setSpindleSpeed < 3000) {
          setSpindleSpeed = 3000;
        }
        else {
          setSpindleSpeed += 1000;
          if (setSpindleSpeed > 24000) setSpindleSpeed = 24000;
        }
      } else {
        setSpindleSpeed -= 1000;
        if (setSpindleSpeed < 3000) {
          setSpindleSpeed = 3000;
        }
      }
      sprintf(sbuf, "M%d S%d", spindleOn ? 3 : 5, setSpindleSpeed);
      btPrintln(sbuf);
      if (!spindleOn) {
        sprintf(sbuf, "M5 S%d", setSpindleSpeed);
        btPrintln(sbuf);
      }
      getGrblState(true);
      reportedSpindleSpeed = setSpindleSpeed; //tot we beter weten
      tftUpdate(false);
    } else { //rState is RotJogspeed
      forceEndJog();
      lastJogCmdXYZ = 0;
      if (dir == 1) {
        if (smallSteps) {
          if (jogSpeed <= 20) ++jogSpeed;
          else jogSpeed *= 1.05;
        } else {
          jogSpeed *= 2.5;
          if (jogSpeed >= 1000) {
            jogSpeed = (jogSpeed / 1000) * 1000;
          } else if (jogSpeed >= 100) {
            jogSpeed = (jogSpeed / 100) * 100;
          } else if (jogSpeed >= 10) {
            jogSpeed = (jogSpeed / 10) * 10;
          }
        }
      } else {
        if (smallSteps) {
          if (jogSpeed <= 20) --jogSpeed;
          else jogSpeed /= 1.05;
        } else if (jogSpeed > 5000) jogSpeed = 5000;
        else {
          jogSpeed /= 2;
          if (jogSpeed >= 1000) {
            jogSpeed = (jogSpeed / 1000) * 1000;
          } else if (jogSpeed >= 100) {
            jogSpeed = (jogSpeed / 100) * 100;
          } else if (jogSpeed >= 10) {
            jogSpeed = (jogSpeed / 10) * 10;
          }
        }
      }
      if (jogSpeed < 2) jogSpeed = 2;
      if (jogSpeed > jogSpeedMax) jogSpeed = jogSpeedMax;
      tftUpdate(false);
    }
  } else if (pState == Menu) {
    if (dir == 1) {
      if (menuChoice > 0) menuChoice--;
    } else if (menuChoice < maxMenu) menuChoice++;
    tftUpdate(false);
  } else if (pState == MenuSpindleSpeed) {
    if (dir == 1) {
      setSpindleSpeed += 1000;
      if (setSpindleSpeed > 24000) setSpindleSpeed = 24000;
    } else {
      setSpindleSpeed -= 1000;
      if (setSpindleSpeed < 3000) setSpindleSpeed = 3000;
    }
  } else if (pState == MenuBrightness) {
    if (dir == 1) {
      if (backLight < 16) {
        backLight++;
      }
    } else if (backLight > 1) {
      backLight--;
    }
    ledcWrite(0, backLight * backLight); // 0-15, 0-255 (with 8 bit resolution)
    tftUpdate(true);
  }
}


void checkConnectBt() {
  static int try_ = 5;
  if (btConnected) {
    try_ = 5;
    return;
  }
  SerialBT.connect();
  if (!SerialBT.connect()) --try_;
  if (try_ == 0) {
    tftPrint(TFT_LEFT, TFT_OBLQ, TFT_RED, TFT_BLACK, 20, 2 * LINEHEIGHT_DEF, 0, "No connection");
    tftPrint(TFT_LEFT, TFT_OBLQ, TFT_RED, TFT_BLACK, 20, 3 * LINEHEIGHT_DEF, 0, "Shutting down");
    delay(2000);
    ESP.restart();
  }
}

void checkBattery() {
  float b = (analogRead(PIN_BATT) - 180) / 1.9;
  if (b > 100) b = 100;
  if (b > battVolt + 1) battVolt += (b - battVolt) / 2;
  if (b < battVolt - 1) battVolt -= (battVolt - b) / 2;
}

void loop() {
  sinceStart = millis() + tExec;
  activeTimer(false);
  checkRotateA();
  if (sinceStart - lastGrblState > updateInterval) {
    checkBattery();
    getGrblState(true);
    checkConnectBt();
    tftUpdate(false);
  }
  checkJoystick();
  if (rdX == 0 && rdY == 0 && rdZ == 0) {
    buttonREMS.update();
    buttonYELLOW.update();
    buttonGREEN.update();
    buttonRED.update();

    if (buttonYELLOW.isClick()) {
      activeTimer(true);
    }
    if (buttonYELLOW.isSingleClick()) {
    }
    if (buttonYELLOW.isLongClick() ) {
      activeTimer(true);
      if (mState == Door && pState == Pendant) { //Alleen resetten vanuit de pemdant-state en niet vanuit menu
        btWrite(24); //Reset
        getGrblState(false);
      } else {
        btWrite(24); //Eerst een reset
        btPrintln((char *)"$X"); //als er een alarm hangt accepteert de controller geen commando's meer, dus dat eerst oplossen met unlock
        btWrite(132); //Door
        pState = Pendant;
        getGrblState(false);
      }
    }
    if (buttonRED.isClick() && rState != RotSpindlespeed) {
      activeTimer(true);
      jState = jsZaxis;
      tftUpdate(true);
    }
    if (buttonRED.isReleased() && rState != RotSpindlespeed) {
      jState = jsXYaxis;
      tftUpdate(true);
    }
    if (buttonRED.isSingleClick()) {
      if (pState != Pendant) {
        pState = Pendant;
        tftUpdate(true);
      }
      else {
        if (mState == Alarm) {
          btPrintln((char *)"$X"); //Unlock
        }
        else if (mState == Run) btWrite('!');
        else if (mState == Hold) btWrite('~');
      }
    }
    if (buttonRED.isLongClick()) {
      if (pState==Menu) powerOffNow=true;
    }
    if (buttonRED.isClick() && pState == Pendant && rState == RotSpindlespeed) {
      sprintf(sbuf, "M%d S%d", spindleOn ? 5 : 3, setSpindleSpeed);
      btPrintln(sbuf);
      getGrblState(true);
    }
    if (buttonGREEN.isLongClick() && pState == Pendant) {
      pState = RotateChoice;
      rState = RotJogspeed;
      tftUpdate(true);
    }
    if (buttonGREEN.isReleased() && pState == RotateChoice) {
      pState = Pendant;
      tftUpdate(true);
    }
    if (buttonREMS.isSingleClick() || (buttonGREEN.isSingleClick())) {
      //Serial.println((String)pState + " " + (String)menuChoice);
      activeTimer(true);
      if (pState == Pendant) {
        pState = Menu;
        menuChoice = quit;
      } else if (pState == Menu) {
        switch (menuChoice) {
          case poweroff:
            powerOffNow=true;
            break;
          case brightness:
            pState = MenuBrightness;
            break;
          case spindleonoff:
            btPrintln(sbuf);
            pState = Pendant;
            break;
          case spindlespeed:
            spindleDisp = setSpindleSpeed;
            pState = MenuSpindleSpeed;
            break;
          case steps:
            smallSteps = !smallSteps;
            pState = Pendant;
            break;
          case unlock: //Unlock
            pState = Pendant;
            btPrintln((char *)"$X");
            break;
          case home: //Home
            pState = Pendant;
            btPrintln((char *)"$H");
            break;
          case resetgrbl: //Reset
            pState = Pendant;
            btWrite(24);
            break;
          case setwxy0:  //XY=0
            pState = MenuConfirm;
            break;
          case setwz0:  //Z=0
            pState = MenuConfirm;
            break;
          case probe:  //probe
            btPrintln((char *)"G21G91");
            btPrintln((char *)"G38.2 Z-10F100");
            btPrintln((char *)"G0Z0.3");
            btPrintln((char *)"G38.2Z-2F10");
            btPrintln((char *)"G10 L20 P1 Z21.35");
            btPrintln((char *)"G91");
            btPrintln((char *)"G0 Z8.65");
            btPrintln((char *)"G90");
            pState = Pendant;
            break;
          case gawxy0:  //naar wXY=0
            //            Serial.println("Restore origin");
            pState = Pendant;
            tftUpdate(true);
            btPrintln((char *)"$J=G53Z0F1000");  //Spindle optrekken
            delay(100);
            waitEndJog();
            btPrintln((char *)"$J=X0 Y0 F5000");
            delay(100);
            getGrblState(false);
            delay(100);
            waitEndJog();
            break;
          default:
          case quit:
            pState = Pendant;
            break;
        }
        //        tft.fillScreen(TFT_BLACK);
      } else if (pState == MenuConfirm) {
        if (menuChoice == setwxy0) {
          btPrintln((char *)"G10 P1 L20 X0 Y0");
        } else if (menuChoice == setwz0) {
          btPrintln((char *)"G10 P1 L20 Z0");
        }
        getGrblState(false);
        pState = Pendant;
      } else if (pState == MenuSpindleSpeed) {
        sprintf(sbuf, "S %d", setSpindleSpeed);
        btPrintln(sbuf);
        pState = Pendant;
      } else if (pState == MenuBrightness) {
        EEPROM.write(0, backLight);
        EEPROM.commit();
        pState = Pendant;
      }
      tftUpdate(true);
    }
  } else {
  }
  //  Serial.print("."); //Check of er puntjes overblijven in de loop
}

void printAxisCoords(float m, float w, byte row) {
  tft.fillRect(18, row * LINEHEIGHT_DEF + 2, 164, LINEHEIGHT_DEF, TFT_BLACK); //clear to eol
  if (m > 0) tftPrint(TFT_LEFT, TFT_TRANSP, TFT_LIGHTBLUE, TFT_BLACK, 18, row * LINEHEIGHT_DEF, 0, "+");
  else if (m < 0) tftPrint(TFT_LEFT, TFT_TRANSP, TFT_LIGHTBLUE, TFT_BLACK, 20, row * LINEHEIGHT_DEF, 0, "-");
  sprintf(sbuf, "%03d.%03d", (int)abs(m) % 1000, (int)(fabsf(m) * 1000) % 1000);
  tftPrint(TFT_LEFT, TFT_TRANSP, TFT_LIGHTBLUE, TFT_BLACK, 27, row * LINEHEIGHT_DEF + 2, 0, sbuf);
  if (w > 0) tftPrint(TFT_LEFT, TFT_TRANSP, TFT_WHITE, TFT_BLACK, 98, row * LINEHEIGHT_DEF, 0, "+");
  else if (w < 0) tftPrint(TFT_LEFT, TFT_TRANSP, TFT_WHITE, TFT_BLACK, 100, row * LINEHEIGHT_DEF, 0, "-");
  sprintf(sbuf, "%03d.%03d", (int)abs(w) % 1000, (int)(fabsf(w) * 1000) % 1000);
  tftPrint(TFT_LEFT, TFT_TRANSP, TFT_WHITE, TFT_BLACK, 108, row * LINEHEIGHT_DEF + 2, 0, sbuf);
}

void btPrintln(char *s) {
  if (btConnected) {
    SerialBT.println(s);
  }
  else mState = Unknwn;
}

void printCircleBlue (byte x, byte y) {
  tft.fillCircle(x, y, 8, pState == RotateChoice ? TFT_MEDIUMBLUE : TFT_DARKBLUE);
}
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

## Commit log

2023-01-25 Add files via upload
    Pictures, STL-files and the scad-files.
    # scad
    The scad-file was made 'quick and dirty'. Be carefull when you change anything.
    # printing
    I printed this in PLA. The case with the smaller bottom flat on the bed and no support.
    [pendantV2.scad]
2023-10-21 Update README.md
    Added hardware for wiring
2023-10-23 updated the edge-cuts to make room for the joystick module
    [pendant v2.kicad_pcb]
